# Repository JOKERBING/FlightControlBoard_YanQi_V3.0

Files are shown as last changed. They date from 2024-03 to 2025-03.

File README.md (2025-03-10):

# YanQi Flight Control Board V3.0

**3 x IMU & Baro & 4 x ESC small size PX4 for MAV research.**

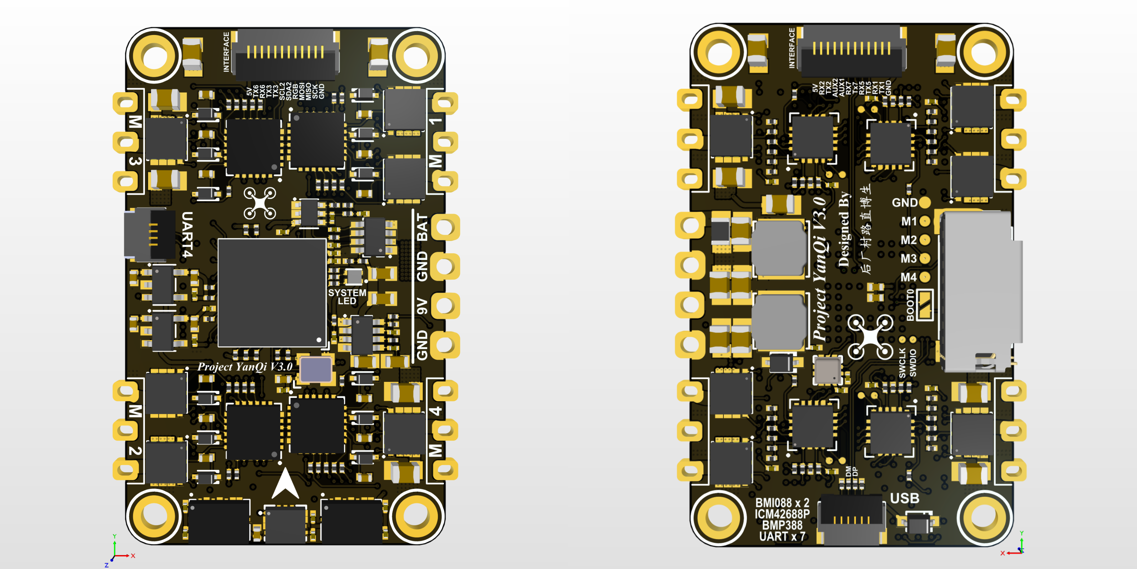
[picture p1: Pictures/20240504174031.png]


## Physical

- Mounting: 20 x 35 mm, Φ 2 mm
- Dimensions: 24 x 39 x 6 mm
- Weight: 4.9 g

## Specifications

- MCU: STM32H743VIH6, 480MHz, 2MB Flash
- IMU: BMI088 + BMI088 + ICM42688P
- Baro: BMP388
- ESC: 4 x Bluejay
- MicroSD Card Slot
- 7 x UART
- 4 x PWM (DShot)
- 1 x External I2C
- 1 x External SPI
- 1 x SRGBLED neopixel
- 1 x SWD
- 2 x ADC (Battery Voltage, Current)
- 2 x AUX
- USB Type-C
- BEC 9V 3A output
- BEC 5V 3A output

## UART Mapping

<style>

.center
{
  width: auto;
  display: table;
  margin-left: auto;
  margin-right: auto;
}

</style>

<div class="center">

| UART | TTY | SerialName | Suggest Funcion | DMA |
| :----: | :-: | :---: | :---: | :-: |
| USART1 | /dev/ttyS0 | GPS1 | | OFF |
| USART2 | /dev/ttyS1 | GPS2 | WIFI module (ESP8266) | ON  |
| USART3 | /dev/ttyS2 | TEL1 | DEBUG | OFF |
| UART4  | /dev/ttyS3 | TEL2 | Offboard PC | ON  |
| UART5  | /dev/ttyS4 |  RC  |  Receiver BlackSheep  | ON  |
| USART6 | /dev/ttyS5 | TEL3 | | OFF |
| UART7  | /dev/ttyS6 | TEL4 | Optical Flow (MTF-01) | ON  |

</div>

## Debug Port

USART3 RX and TX are configured for use as the **System Console**.

## Getting Start

### Compile Locally

Follow the PX4 standard approach.

#### Bootloader:

```shell
make UCAS_YanQiH7_bootloader
```

#### Firmware:

```shell
make UCAS_YanQiH7_default
```

### Burn Bootloader & Firmware

#### Bootloader:

**Method 1：**

 To enter DFU mode, pull up BOOT0 while connecting the USB cable to your computer.

```shell
make UCAS_YanQiH7_bootloader upload
```

**Method 2：**

 To enter DFU mode, pull up BOOT0 while connecting the USB cable to your computer.

```shell
dfu-util -a 0 --dfuse-address 0x08000000 -D ./build/UCAS_YanQiH7_bootloader/UCAS_YanQiH7_bootloader.bin
```

If the burning tool is not installed, install the dfu util burning toolkit first.

```
sudo apt install dfu-util
```

#### Firmware:

**Method 1：**

```shell
make UCAS_YanQiH7_default upload
```

Connect the flight controller directly to your computer via USB.

The firmware will then proceed through a number of upgrade steps (downloading new firmware, erasing old firmware etc.). Each step is printed to the screen.

Once the firmware has completed loading, the device/vehicle will reboot and reconnect.

**Method 2：**

Start QGroundControl and connect the vehicle.

Select **"Q" icon** > **Vehicle Setup** > **Firmware** (sidebar) to open Firmware Setup.

Connect the flight controller directly to your computer via USB.

Check **Advanced settings** and select the version from the dropdown list.

Select the **Custom Firmware file...** option to install the custom firmware for the flight controller (autodetected).

Click the **OK** button to start the update.

The firmware will then proceed through a number of upgrade steps (downloading new firmware, erasing old firmware etc.). Each step is printed to the screen and overall progress is displayed on a progress bar.

Once the firmware has completed loading, the device/vehicle will reboot and reconnect.

## Setting Up PX4 Configuration Settings

### Power

### MAVLink

### Receiver

## TODO

- [ ]  stable SRGBLED driver based on srgbled_dma

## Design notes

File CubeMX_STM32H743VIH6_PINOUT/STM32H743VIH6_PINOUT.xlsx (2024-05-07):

 |  |  |  |  | 只能从系统给定的方案中选 |  |  |  |  |  |  |  | 所使用的GPIO不能重复 | 所使用的外部中断号不能重复，因为一个外部中断上只能挂一个GPIO
 | 板内资源 | 板外资源 | 资源名称 | GPIO功能 | GPIO方案1 | GPIO方案2 | GPIO方案3 | GPIO方案4 | GPIO方案5 | GPIO方案6 | GPIO方案7 | 片选和外部中断GPIO | GPIO | 所使用的外部中断号 | CubeMX检查 | 原理图检查
SPI |  | 引出 | SPI1 | MOSI | PA7 | PB5 | PD7 |  |  |  |  |  |  |  | √ | √
 |  |  |  | MISO | PA6 | PB4 | PG9 |  |  |  |  |  |  |  | √ | √
 |  |  |  | SCK | PA5 | PB3 | PG11 |  |  |  |  |  |  |  | √ | √
 | BMI088 |  | SPI2 | MOSI | PB15 | PC1 | PC3 | PI3 |  |  |  | Gyro_CS | PC13 |  | √ | √
 |  |  |  | MISO | PB14 | PC2 | PI2 |  |  |  |  | Accel_CS | PC3 |  | √ | √
 |  |  |  | SCK | PA12 | PA9 | PB10 | PB13 | PD3 | PI1 |  | Gyro_Data_Ready | PE3 | EXTI3 | √ | √
 |  |  |  |  |  |  |  |  |  |  |  | Accel_Data_Ready | PE4 | EXTI4 | √ | √
 | ICM42688P |  | SPI3 | MOSI | PD6 | PC12 | PB2 | PB5 |  |  |  |  |  |  | √ | √
 |  |  |  | MISO | PB4 | PC11 |  |  |  |  |  | CS | PE0 |  | √ | √
 |  |  |  | SCK | PB3 | PC10 |  |  |  |  |  | Data_Ready | PE1 | EXTI1 | √ | √
 | BMI088 |  | SPI4 | MOSI | PE14 | PE6 |  |  |  |  |  | Gyro_CS | PB6 |  | √ | √
 |  |  |  | MISO | PE13 | PE5 |  |  |  |  |  | Accel_CS | PD4 |  | √ | √
 |  |  |  | SCK | PE12 | PE2 |  |  |  |  |  | Gyro_Data_Ready | PD5 | EXTI5 | √ | √
 |  |  |  |  |  |  |  |  |  |  |  | Accel_Data_Ready | PD6 | EXTI6 | √ | √
 | 不使用 |  | SPI5 | MOSI | PF11 | PF9 | PJ10
 |  |  |  | MISO | PF8 | PH7 | PJ11
 |  |  |  | SCK | PF7 | PH6 | PK0
 | 不使用 |  | SPI6 | MOSI | PG14 | PA7 | PB5
 |  |  |  | MISO | PG12 | PA6 | PB4
 |  |  |  | SCK | PG13 | PA5 | PB3
I2C | BMP388 |  | I2C1 | SDA | PB7 | PB9 |  |  |  |  |  | Data_Ready | PB7 | EXTI7 | √ | √
 |  |  |  | SCL | PB6 | PB8 |  |  |  |  |  |  |  |  | √ | √
 |  | 引出 | I2C2 | SDA | PB11 | PF0 | PH5 |  |  |  |  |  |  |  | √ | √
 |  |  |  | SCL | PB10 | PF1 | PH4 |  |  |  |  |  |  |  | √ | √
 | 不使用 |  | I2C3 | SDA | PC9 | PH8
 |  |  |  | SCL | PA8 | PH7
 | 不使用 |  | I2C4 | SDA | PD13 | PF15 | PH12 | PB7 | PB9
 |  |  |  | SCL | PD12 | PF14 | PH11 | PB6 | PB8
UART |  |  | USART1 | RX | PB15 | PA10 | PB7 |  |  |  |  |  |  |  | √ | √
 |  |  |  | TX | PB14 | PA9 | PB6 |  |  |  |  |  |  |  | √ | √
 |  |  | USART2 | RX | PA3 | PD6 |  |  |  |  |  |  |  |  | √ | √
 |  |  |  | TX | PA2 | PD5 |  |  |  |  |  |  |  |  | √ | √
 |  |  | USART3 | RX | PB11 | PC11 | PD9 |  |  |  |  |  |  |  | √ | √
 |  |  |  | TX | PB10 | PC10 | PD8 |  |  |  |  |  |  |  | √ | √
 |  | Offboard电脑 | UART4 | RX | PA11 | PA1 | PB8 | PC11 | PD0 | PH14 | PI9 |  |  |  | √ | √
 |  |  |  | TX | PA12 | PA0 | PB9 | PC10 | PD1 | PH13 |  |  |  |  | √ | √
 |  |  | UART5 | RX | PB12 | PB5 | PD2 |  |  |  |  |  |  |  | √ | √
 |  |  |  | TX | PB13 | PB6 | PC12 |  |  |  |  |  |  |  | √ | √
 |  |  | USART6 | RX | PC7 | PG9 |  |  |  |  |  |  |  |  | √ | √
 |  |  |  | TX | PC6 | PG14 |  |  |  |  |  |  |  |  | √ | √
 |  |  | UART7 | RX | PA8 | PB3 | PE7 | PF6 |  |  |  |  |  |  | √ | √
 |  |  |  | TX | PA15 | PB4 | PE8 | PF7 |  |  |  |  |  |  | √ | √
 | 不使用 |  | UART8 | RX | PE0 | PJ9
 |  |  |  | TX | PE1 | PJ8
MOTOR |  | PWM/DSHOT | CH1 | GPIO_TIM4_CH1OUT_2 | PD12 |  |  |  |  |  |  |  |  |  | √ | √
 |  |  | CH2 | GPIO_TIM4_CH2OUT_2 | PD13 |  |  |  |  |  |  |  |  |  | √ | √
 |  |  | CH3 | GPIO_TIM4_CH3OUT_2 | PD14 |  |  |  |  |  |  |  |  |  | √ | √
 |  |  | CH4 | GPIO_TIM4_CH4OUT_2 | PD15 |  |  |  |  |  |  |  |  |  | √ | √
USB |  | USB | USB_FS | DM | PA11 |  |  |  |  |  |  |  |  |  | √ | √
 |  |  |  | DP | PA12 |  |  |  |  |  |  |  |  |  | √ | √
USB Detection |  |  | GPIO_INPUT |  | PA15 |  |  |  |  |  |  |  |  |  | √ | √
SD | SD Card |  | SDMMC | D0 | PC8 |  |  |  |  |  |  |  |  |  | √ | √
 |  |  |  | D1 | PC9 |  |  |  |  |  |  |  |  |  | √ | √
 |  |  |  | D2 | PC10 |  |  |  |  |  |  |  |  |  | √ | √
 |  |  |  | D3 | PC11 |  |  |  |  |  |  |  |  |  | √ | √
 |  |  |  | CK | PC12 |  |  |  |  |  |  |  |  |  | √ | √
 |  |  |  | CMD | PD2 |  |  |  |  |  |  |  |  |  | √ | √
BATTERY | BAT_V |  | ADC1 | ADC1_IN4 | PC4 |  |  |  |  |  |  |  |  |  | √ | √
 | BAT_I |  | ADC1 | ADC1_IN8 | PC5 |  |  |  |  |  |  |  |  |  | √ | √
LSE | 不使用 |  | OSC32 | OSC_IN | PC14
 |  |  |  | OSCOUT | PC15
HSE | 16MHz |  | OSC | OSC_IN | PH0 |  |  |  |  |  |  |  |  |  | √ | √
 |  |  |  | OSCOUT | PH1
LED |  |  | GPIO_OUTPUT | Red | PC0 |  |  |  |  |  |  |  |  |  | √ | √
 |  |  |  | Green | PA0 |  |  |  |  |  |  |  |  |  | √ | √
 |  |  |  | Blue | PA1 |  |  |  |  |  |  |  |  |  | √ | √
SRGBLED |  |  | TIM1 | GPIO_TIM1_CH1OUT_2 | PE9 |  |  |  |  |  |  |  |  |  | √ | √
AUX |  |  |  | AUX1 | PB0 |  |  |  |  |  |  |  |  |  | √ | √
 |  |  |  | AUX2 | PB1 |  |  |  |  |  |  |  |  |  | √ | √
DEBUG |  |  | SWD | SWDIO | PA13 |  |  |  |  |  |  |  |  |  | √ | √
 |  |  |  | SWCLK | PA14 |  |  |  |  |  |  |  |  |  | √ | √

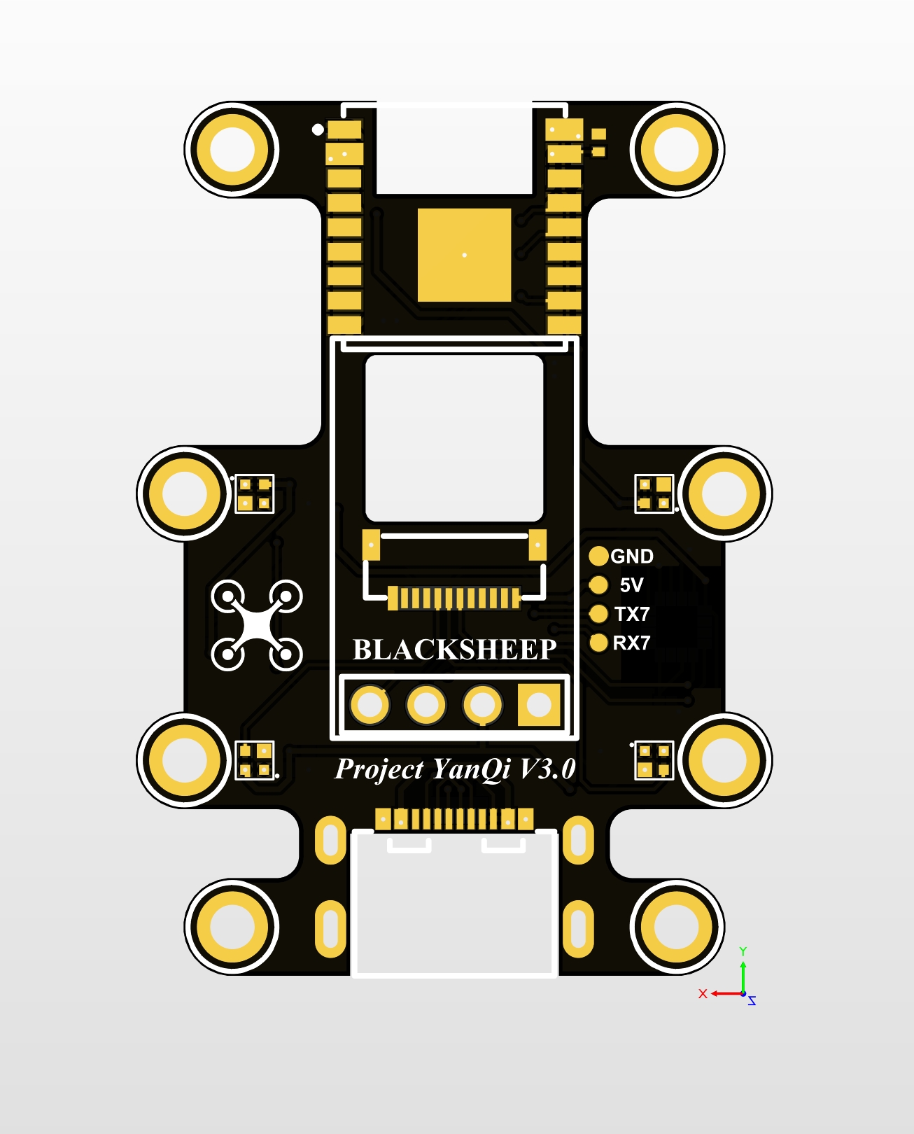
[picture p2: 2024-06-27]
3D_Model/PayloadBoard_BOTTOM.png

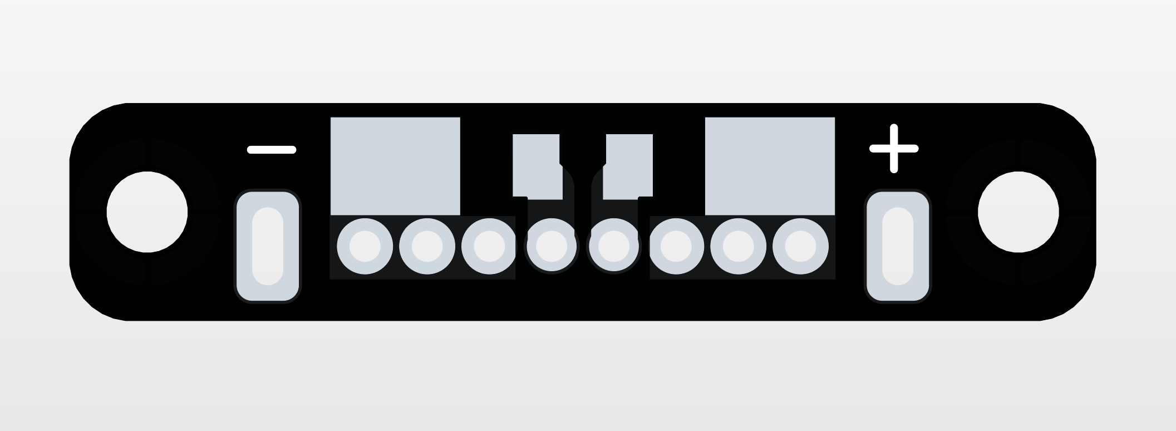
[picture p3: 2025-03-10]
3D_Model/BatteryBoard_BOTTOM.png

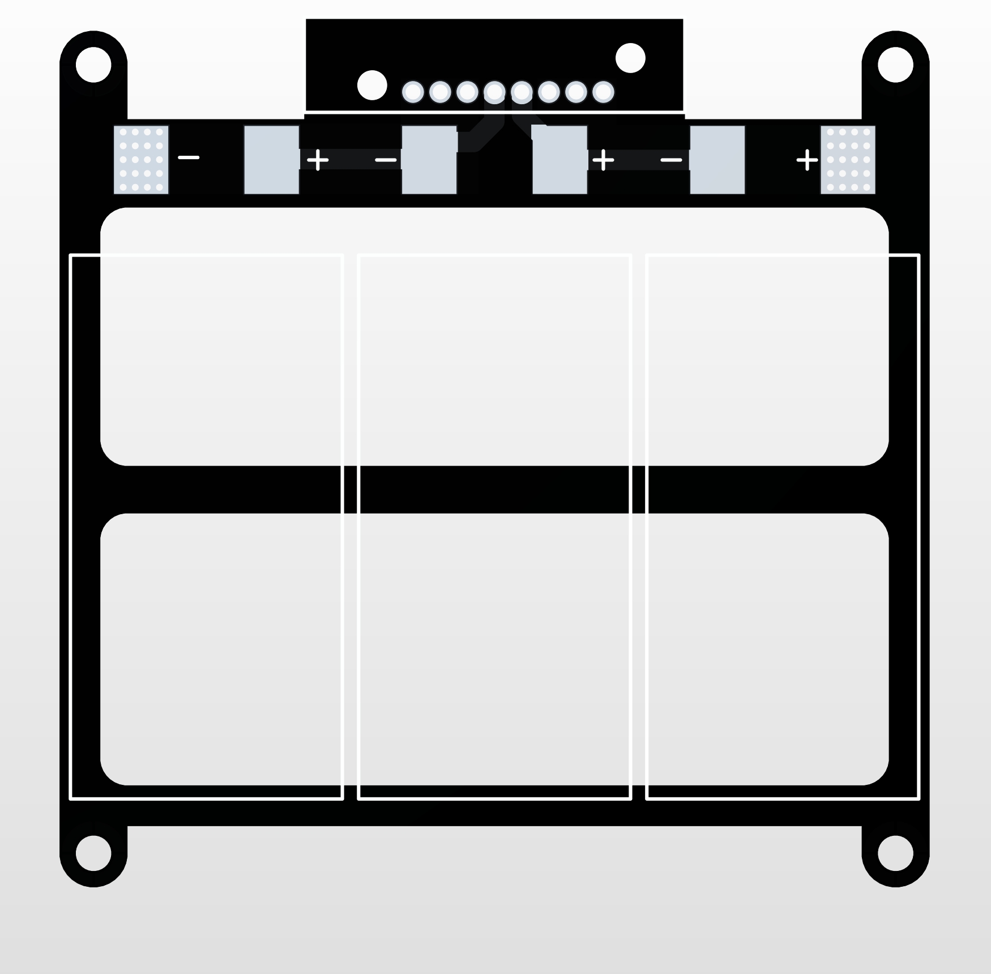
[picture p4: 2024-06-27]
3D_Model/BatteryBaseBoard_BOTTOM.png

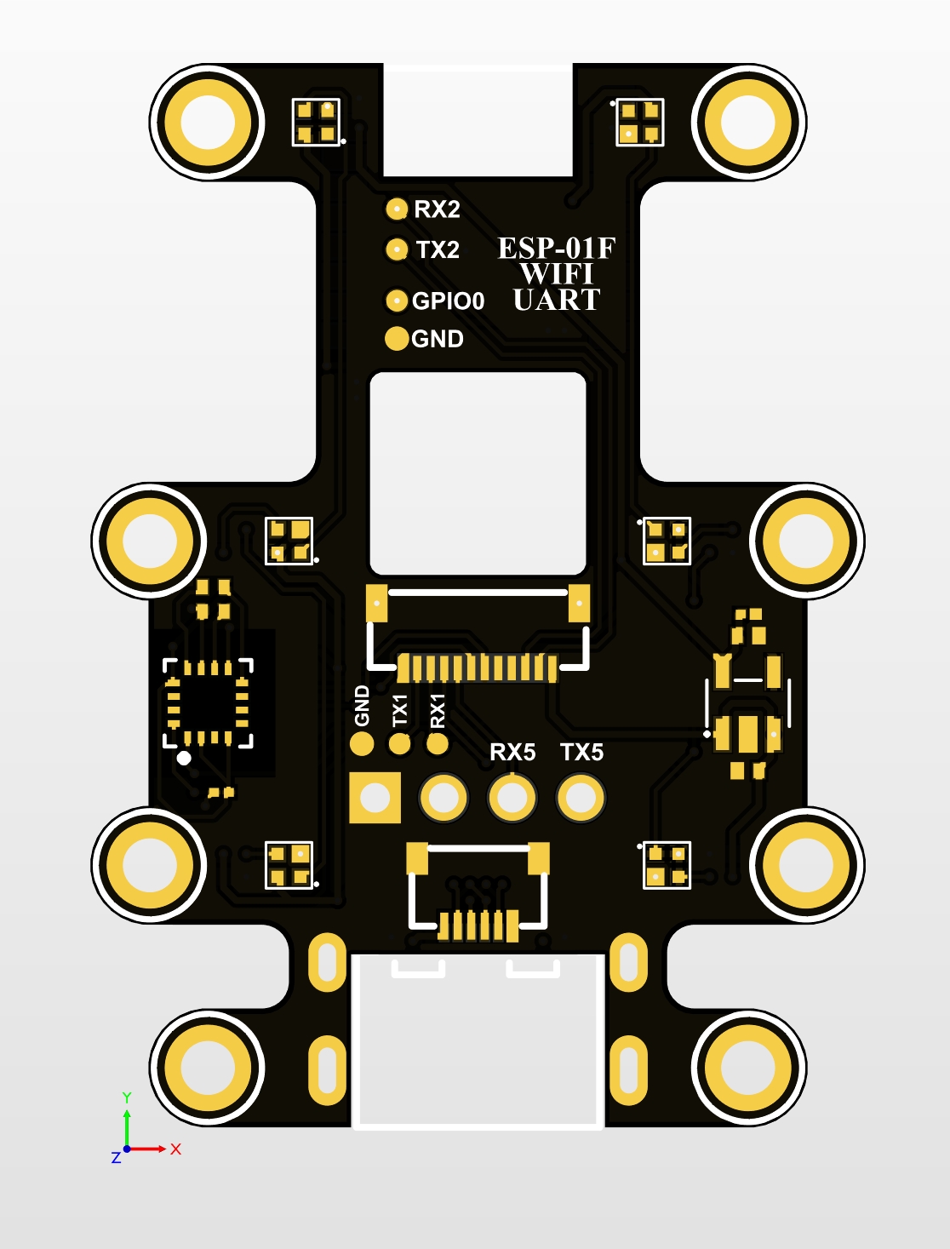
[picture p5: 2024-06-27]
3D_Model/PayloadBoard_TOP.png

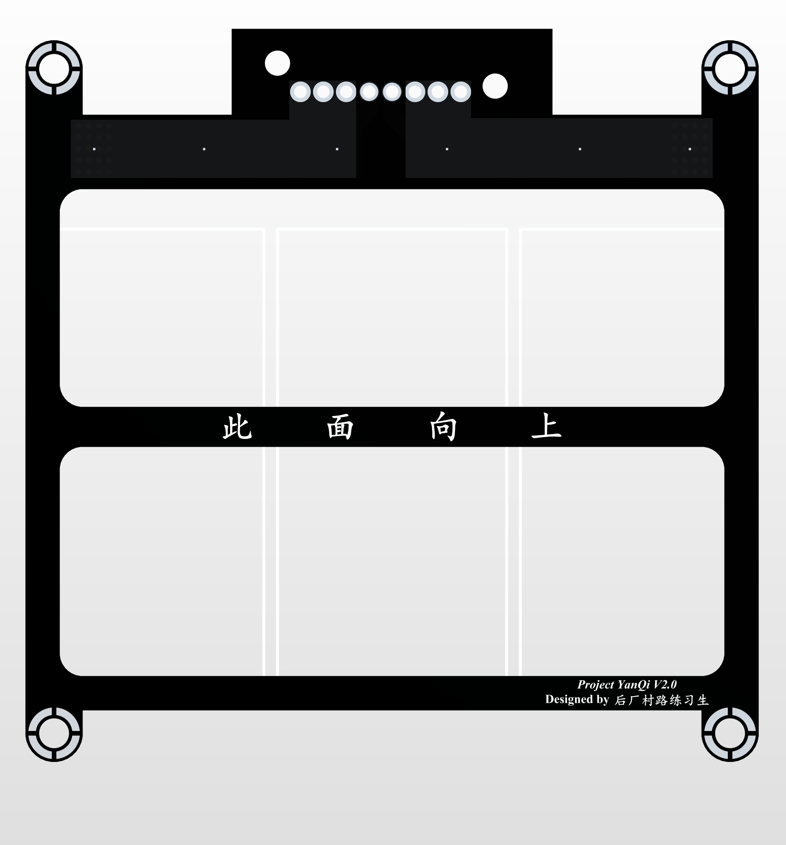
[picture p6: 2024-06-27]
3D_Model/BatteryBaseBoard_TOP.png

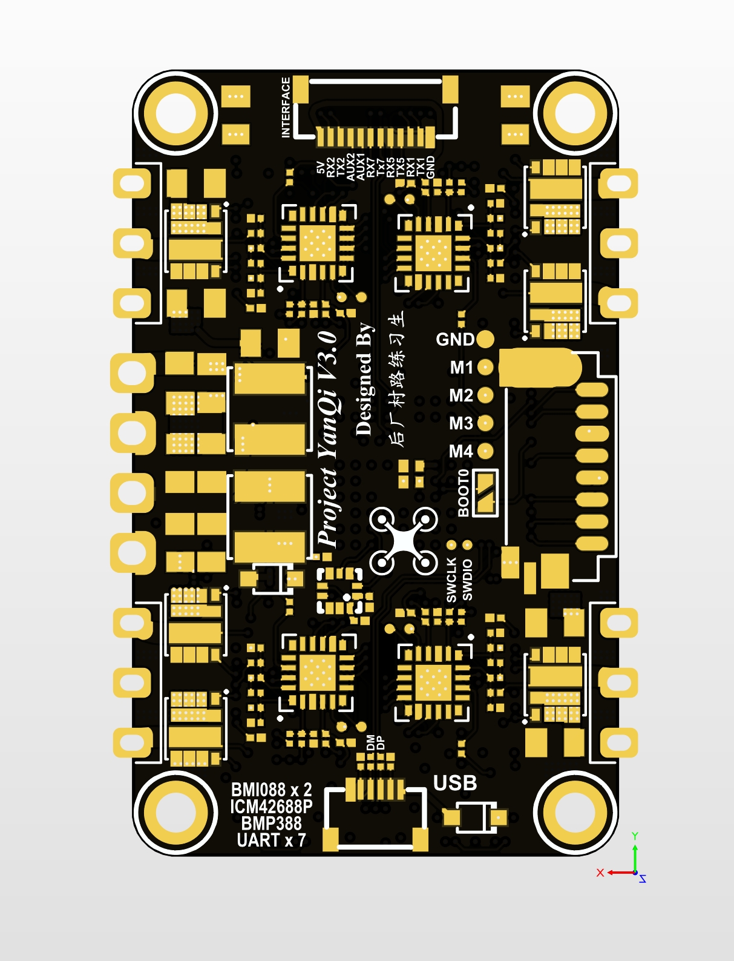
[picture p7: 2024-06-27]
3D_Model/FlightControlBoard_BOTTOM.png

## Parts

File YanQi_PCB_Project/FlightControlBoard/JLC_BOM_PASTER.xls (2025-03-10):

型号 | 封装 | 位号 | 元件编号
5.1kΩ | R0201 | R83,R84 | C158467
BMI088 | LGA-16_L4.5-W3.0-P0.50-BL | U11,U12 | C194919
47kΩ | R0201 | R26,R28,R30,R32,R34,R36,R38,R40,R42,R44,R46,R48 | C138139
RT9013-33GB | SOT-23-5 | U16,U17 | C47773
STM32H743VIH6 | BGA-100_L8.0-W8.0-P0.80-R10-C10-BL | U1 | C964146
1nF | C0201 | C55 | C161371
1uF | C0402 | C17,C18,C19,C20,C21,C22,C23,C24,C25,C26,C27,C28,C48,C49,C51,C52 | C52923
1N5819WS | SOD-323 | D13,D14 | C191023
X1G004171002700 | OSC-SMD_4P-L2.5-W2.0-BL | X1 | C255993
INA199A1DCKR | SOT-323-6 | U18 | C59135
2.2uF | C0402 | C2,C3,C34 | C342966
1kΩ | R0201 | R6,R7,R8,R9 | C138165
FC-B1010RGBT-HG | LED-ARRAY-SMD_4P-L1.0-W1.0-TR-RD | LED1 | C158099
22uF | C0603 | C39,C40,C41,C42 | C2762594
FD6288Q | QFN-24_L4.0-W4.0-P0.50-BL-EP2.6 | U6,U7,U8,U9 | C328453
100nF | C0201 | C5,C7,C8,C9,C10,C11,C12,C13,C14,C15,C16,C29,C30,C32,C33,C35,C36,C37,C38,C43,C44,C45,C46,C47,C50,C53,C54 | C160831
BMP388 | LGA-10 | U13 | C779278
15pF | C0201 | C6 | C3034519
AON7934 | DFN-8 | Q1,Q2,Q3,Q4,Q5,Q6,Q7,Q8,Q9,Q10,Q11,Q12 | C485677
140kΩ | R0201 | R89 | C966893
22uF | C0805 | C56,C57,C58,C59,C60,C61,C62,C63,C64,C65,C66,C67,C68,C69,C70,C71,C72,C73 | C45783
MP2225GJ-Z | SOT-23-8 | U14,U15 | C9900010483
ICM-42688-P | LGA-14_L3.0-W2.5-P0.50-TL | U10 | C1850418
10kΩ | R0201 | R1,R2,R3,R4,R5,R10,R11,R12,R13,R14,R15,R16,R17,R18,R19,R20,R21,R22,R23,R24,R25,R78,R79,R80,R81,R82,R87,R88,R93 | C102690
10mΩ | R0805 | R96 | C163089
FH34SRJ-4S-0.5SH(50) | FFC-SMD_4P-P0.50_FH34SRJ-4S-0.5SH | FPC4 | C596732
10nF | C0201 | C31 | C161481
22Ω | R0201 | R50,R51,R52,R53,R54,R55,R56,R57,R58,R59,R60,R61,R62,R63,R64,R65,R66,R67,R68,R69,R70,R71,R72,R73,R85,R86 | C155743
74kΩ | R0201 | R90 | C851792
FH34SRJ-12S-0.5SH(50) | FFC-SMD_12P-P0.50_FH34SRJ-12S-0.5SH | FPC1,FPC3 | C424659
FH34SRJ-6S-0.5SH(50) | FFC-SMD_6P-P0.50_FH34SRJ-6S-0.5SH | FPC2 | C224194
100kΩ | R0201 | R91,R92,R94 | C270364
TF-027-H300 | TF-SMD_HYCW104-TF08-375B | SD1 | C5310495
FHD4020S-100MT | IND-SMD_L4.0-W4.0 | L1 | C602032
FHD4020S-4R7MT | IND-SMD_L4.0-W4.0 | L2 | C602031
4.7kΩ | R0201 | R27,R29,R31,R33,R35,R37,R39,R41,R43,R45,R47,R49,R74,R75,R76,R77 | C270346
1uF | C0201 | C4 | C237278
4.7uF | C0402 | C1 | C23733
EFM8BB21F16G | QFN-20_L3.0-W3.0-P0.50-BL-EP1.7_EFM8BB21F16G | U2,U3,U4,U5 | C80713
56Ω | R0201 | R95 | C138095
1N4148WTT4 | SOD-523 | D1,D2,D3,D4,D5,D6,D7,D8,D9,D10,D11,D12 | C68948
MotorPad | MOTORHALFHOLE | P16,P17,P18,P19,P20,P21,P22,P23,P24,P25,P26,P27 | NC
Power_Pad | POWERHALFHOLE | P28,P29,P30,P31 | NC
BurnPad | BurnPad_0.5mm | P1,P3,P4,P5,P6,P7,P8,P9,P10,P11 | NC
M2_HOLE | M2_HOLE | H1,H2,H3,H4 | NC
ShortCircuitPad | ShortCircuitPad | P2 | NC
BurnPad | BurnPad_0.8mm | P12,P13,P14,P15,P32 | NC

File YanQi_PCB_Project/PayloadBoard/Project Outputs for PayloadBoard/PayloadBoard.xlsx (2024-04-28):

Comment | Designator | Footprint | Quantity | Value | Supplier Part
1uF | C1, C2, C5 | C0402 | 3 | 1uF | C52923
100nF | C3, C4 | C0201 | 2 | 100nF | C160831
0.22uF | C6 | C0402 | 1 | 0.22uF | C16772
4.7uF | C7 | C0402 | 1 | 4.7uF | C23733
FH34SRJ-12S-0.5SH(50) | FPC1, FPC2 | FFC-SMD_12P-P0.50_FH34SRJ-12S-0.5SH | 2 |  | C424659
FH34SRJ-6S-0.5SH(50) | FPC3 | FFC-SMD_6P-P0.50_FH34SRJ-6S-0.5SH | 1 |  | C224194
M2_HOLE | H1, H2, H3, H4, H5, H6, H7, H8 | M2_HOLE | 8 |  | NC
BLACKSHEEP | M1 | BLACKSHEEP | 1 |  | NC
BurnPad | P1, P2, P3, P4, P5, P6, P7, P8, P9, P10, P11 | BurnPad_0.8mm | 11 |  | NC
XL-1010RGBC-WS2812B | RGB1, RGB2, RGB3, RGB4, RGB5, RGB6, RGB7, RGB8, RGB9, RGB10 | LED-SMD_4P-L1.0-W1.0-TL_XL-1010RGBC-WS2812B | 10 |  | C5349953
RT9013-33GB | U1 | SOT-23-5 | 1 |  | C47773
ESP-01F-2M | U2 | WIFIM-SMD_ESP-01F-2M | 1 | 2.4GHz | C2764054
QMC5883L | U3 | LGA-16_L3.0-W3.0-P0.50-BL_SQ | 1 |  | C976032
918-418K2024S40000 | USBC1 | USB-C-SMD_TYPE-C-USB-4 | 1 |  | C168688

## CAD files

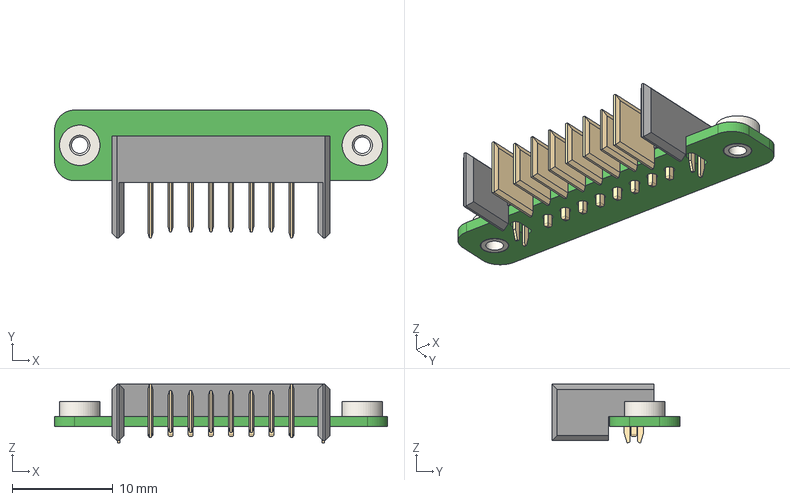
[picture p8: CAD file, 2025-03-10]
3D_Model/BatteryBoard.step
33.0 x 12.7 x 5.80 mm
M2x4x1.5+2.5x1 x 2
BAT_8P_M

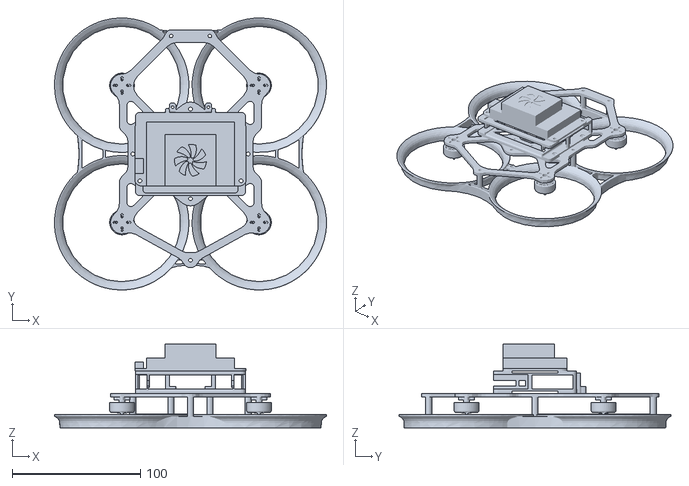
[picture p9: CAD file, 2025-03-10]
Gazebo_Model/microfly.stl
212.5 x 212.5 x 65.5

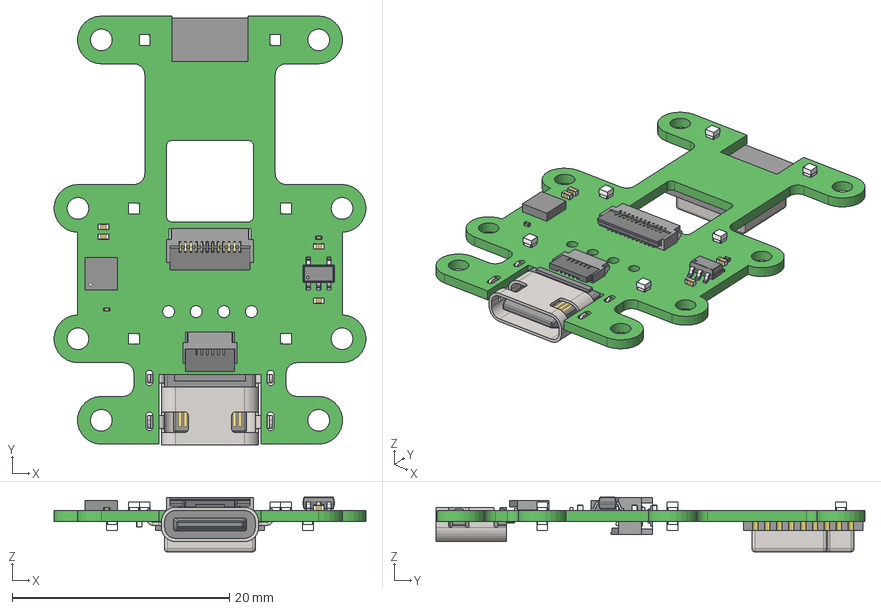
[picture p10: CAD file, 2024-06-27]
3D_Model/PayloadBoard.step
28.7 x 39.5 x 5.06 mm

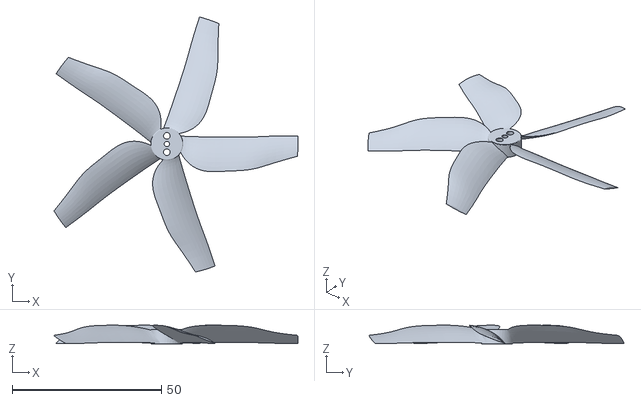
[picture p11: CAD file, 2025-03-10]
Gazebo_Model/microfly_3.5_prpo_cw.stl
81.9 x 85.6 x 6.27

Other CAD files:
Gazebo_Model/microfly_3.5_prpo_ccw.stl
3D_Model/Battery.f3d
3D_Model/BatteryBase.f3d
3D_Model/BatteryBaseBoard.f3d
3D_Model/BatteryBoard.f3d
3D_Model/BatteryCase.f3d
3D_Model/BlackSheep_nano_RX.f3d
3D_Model/Camera_D435i_Frame.f3d
3D_Model/Camera_D435i_PCB.f3d
3D_Model/CarbonFiberBoard v13.f3d
3D_Model/CarbonFiberBoard.f3d
3D_Model/CarbonFiberBoardDown.f3d
3D_Model/FAN.f3d
3D_Model/FlightControlBoard.f3d
3D_Model/M2x10_POST.f3d
3D_Model/M2x15_POST.f3d
3D_Model/M2x5_POST.f3d
3D_Model/MTF-01_Optical_Flow.f3d
3D_Model/Motor.f3d
3D_Model/P3767-pcba-envelop.f3d
3D_Model/PayloadBoard.f3d
3D_Model/Propeller_CCW.f3d
3D_Model/Propeller_CW.f3d
3D_Model/Shock_Pad.f3d

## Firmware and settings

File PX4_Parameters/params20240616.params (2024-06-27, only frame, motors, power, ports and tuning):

1	1	BAT1_A_PER_V	1.936521768569946289	9
1	1	BAT1_CAPACITY	-1.000000000000000000	9
1	1	BAT1_I_CHANNEL	-1	6
1	1	BAT1_N_CELLS	3	6
1	1	BAT1_R_INTERNAL	-1.000000000000000000	9
1	1	BAT1_SOURCE	0	6
1	1	BAT1_V_CHANNEL	-1	6
1	1	BAT1_V_CHARGED	4.449999809265136719	9
1	1	BAT1_V_DIV	10.926829338073730469	9
1	1	BAT1_V_EMPTY	3.000000000000000000	9
1	1	BAT1_V_LOAD_DROP	0.300000011920928955	9
1	1	BAT_AVRG_CURRENT	15.000000000000000000	9
1	1	BAT_CRIT_THR	0.070000000298023224	9
1	1	BAT_EMERGEN_THR	0.050000000745058060	9
1	1	BAT_LOW_THR	0.150000005960464478	9
1	1	BAT_N_CELLS	3	6
1	1	BAT_V_CHARGED	4.050000190734863281	9
1	1	BAT_V_EMPTY	3.500000000000000000	9
1	1	BAT_V_LOAD_DROP	0.300000011920928955	9
1	1	BAT_V_OFFS_CURR	0.000000000000000000	9
1	1	CA_ROTOR0_PX	0.150000005960464478	9
1	1	CA_ROTOR0_PY	0.150000005960464478	9
1	1	CA_ROTOR1_PX	-0.150000005960464478	9
1	1	CA_ROTOR1_PY	-0.150000005960464478	9
1	1	CA_ROTOR2_KM	-0.050000000745058060	9
1	1	CA_ROTOR2_PX	0.150000005960464478	9
1	1	CA_ROTOR2_PY	-0.150000005960464478	9
1	1	CA_ROTOR3_KM	-0.050000000745058060	9
1	1	CA_ROTOR3_PX	-0.150000005960464478	9
1	1	CA_ROTOR3_PY	0.150000005960464478	9
1	1	CA_ROTOR_COUNT	4	6
1	1	MC_PITCHRATE_D	0.002600000007078052	9
1	1	MC_PITCHRATE_FF	0.000000000000000000	9
1	1	MC_PITCHRATE_I	0.250000000000000000	9
1	1	MC_PITCHRATE_K	0.400000005960464478	9
1	1	MC_PITCHRATE_MAX	220.000000000000000000	9
1	1	MC_PITCHRATE_P	0.150000005960464478	9
1	1	MC_PITCH_P	12.000000000000000000	9
1	1	MC_ROLLRATE_D	0.002799999900162220	9
1	1	MC_ROLLRATE_FF	0.000000000000000000	9
1	1	MC_ROLLRATE_I	0.250000000000000000	9
1	1	MC_ROLLRATE_K	0.349999994039535522	9
1	1	MC_ROLLRATE_MAX	220.000000000000000000	9
1	1	MC_ROLLRATE_P	0.150000005960464478	9
1	1	MC_ROLL_P	12.000000000000000000	9
1	1	MC_YAWRATE_D	0.002000000094994903	9
1	1	MC_YAWRATE_FF	0.000000000000000000	9
1	1	MC_YAWRATE_I	0.200000002980232239	9
1	1	MC_YAWRATE_K	1.450000047683715820	9
1	1	MC_YAWRATE_MAX	360.000000000000000000	9
1	1	MC_YAWRATE_P	0.200000002980232239	9
1	1	MC_YAW_P	10.000000000000000000	9
1	1	MC_YAW_WEIGHT	0.400000005960464478	9
1	1	MOT_ORDERING	0	6
1	1	MOT_POLE_COUNT	12	6
1	1	MOT_SLEW_MAX	0.000000000000000000	9
1	1	SYS_AUTOSTART	4001	6

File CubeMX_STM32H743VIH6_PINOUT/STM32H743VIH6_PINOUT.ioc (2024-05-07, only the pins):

Mcu.UserName=STM32H743VIHx
PA0.GPIO_Label=LED_GREEN
PA0.Signal=GPIO_Output
PA1.GPIO_Label=LED_BLUE
PA1.Signal=GPIO_Output
PA10.Signal=USART1_RX
PA11.Signal=USB_OTG_FS_DM
PA12.Signal=USB_OTG_FS_DP
PA2.Signal=USART2_TX
PA3.Signal=USART2_RX
PA5.Signal=SPI1_SCK
PA6.Signal=SPI1_MISO
PA7.Signal=SPI1_MOSI
PA9.Signal=USART1_TX
PB0.GPIO_Label=AUX1
PB0.Signal=GPIO_Output
PB1.GPIO_Label=AUX2
PB1.Signal=GPIO_Output
PB10.Signal=I2C2_SCL
PB11.Signal=I2C2_SDA
PB12.Signal=UART5_RX
PB13.Signal=UART5_TX
PB5.Signal=SPI3_MOSI
PB6.GPIO_Label=SPI4_Gyro_CS
PB6.Signal=GPIO_Output
PB7.GPIO_Label=I2C1_Data_Ready
PB7.Signal=GPXTI7
PB8.Signal=I2C1_SCL
PB9.Signal=I2C1_SDA
PC0.GPIO_Label=LED_RED
PC0.Signal=GPIO_Output
PC1.Signal=SPI2_MOSI
PC10.Signal=SDMMC1_D2
PC11.Signal=SDMMC1_D3
PC12.Signal=SDMMC1_CK
PC13.GPIO_Label=SPI2_Gyro_CS
PC13.Signal=GPIO_Output
PC2_C.Signal=SPI2_MISO
PC3_C.GPIO_Label=SPI2_Accel_CS
PC3_C.Signal=GPIO_Output
PC4.GPIO_Label=BAT_V
PC4.Signal=ADCx_INP4
PC5.GPIO_Label=BAT_I
PC5.Signal=ADCx_INP8
PC6.Signal=USART6_TX
PC7.Signal=USART6_RX
PC8.Signal=SDMMC1_D0
PC9.Signal=SDMMC1_D1
PD0.Signal=UART4_RX
PD1.Signal=UART4_TX
PD12.GPIO_Label=PWM1
PD12.Signal=S_TIM4_CH1
PD13.GPIO_Label=PWM2
PD13.Signal=S_TIM4_CH2
PD14.GPIO_Label=PWM3
PD14.Signal=S_TIM4_CH3
PD15.GPIO_Label=PWM4
PD15.Signal=S_TIM4_CH4
PD2.Signal=SDMMC1_CMD
PD3.Signal=SPI2_SCK
PD4.GPIO_Label=SPI4_Accel_CS
PD4.Signal=EVENTOUT
PD5.GPIO_Label=SPI4_Gyro_Data_Ready
PD5.Signal=GPXTI5
PD6.GPIO_Label=SPI4_Accel_Data_Ready
PD6.Signal=GPXTI6
PD8.Signal=USART3_TX
PD9.Signal=USART3_RX
PE0.GPIO_Label=SPI3_CS
PE0.Signal=GPIO_Output
PE1.GPIO_Label=SPI3_Data_Ready
PE1.Signal=GPXTI1
PE2.Signal=SPI4_SCK
PE3.GPIO_Label=SPI2_Gyro_Data_Ready
PE3.Signal=GPXTI3
PE4.GPIO_Label=SPI2_Accel_Data_Ready
PE4.Signal=GPXTI4
PE5.Signal=SPI4_MISO
PE6.Signal=SPI4_MOSI
PE7.Signal=UART7_RX
PE8.Signal=UART7_TX
PE9.GPIO_Label=SRGBLED
PE9.Signal=S_TIM1_CH1

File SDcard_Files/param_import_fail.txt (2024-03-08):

HW arch: HKUST_NXT
FW git-hash: 59a22c1904ec3d1d598ea04cc48ff90d5cf7bea0
FW version: 1.13.2 0 (17629696)
FW git-branch: pre_release_v1.2.x_firmware
OS: NuttX
OS version: Release 11.0.0 (184549631)
OS git-hash: 91bece51afbe7da9db12e3695cdbb4f4bba4bc83
Build datetime: Jun  1 2023 15:25:53
Build uri: localhost
Build variant: default
Toolchain: GNU GCC, 9.3.1 20200408 (release)
PX4GUID: 000600000000383632333131510e003d0029
MCU: STM32H7[4|5]xxx, rev. V
INFO  [param] selected parameter default file /fs/microsd/params
ERROR [param] open '/fs/microsd/params' failed (2)
ERROR [init] param import failed
ERROR [param] open '/fs/microsd/params' failed (2)
dmesg [23:100]
cp [29:100]

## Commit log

2024-03-08 更新PINOUT文件
    [STM32H743VIH6_PINOUT.xlsx, param_import_fail.txt]
2024-04-28 提交更新
    [BatteryBaseBoard.PrjPcb, BatteryBaseBoard.SchDoc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]
